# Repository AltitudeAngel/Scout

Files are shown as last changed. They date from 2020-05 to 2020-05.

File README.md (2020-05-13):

# Scout

_Scout_ is an open-source project consisting of hardware and firmware that enables software developers, drone manufacturers and commercial drone pilots to quickly develop drone solutions that collect (using an extensible chip architecture) information about the location of the device (or, the vehicle to which the device is attached), and use cellular communications technologies to both send that position and other sensor data to and receive navigation data back from unmanned traffic management (UTM) system.

Scout's *not* presently aimed at drone pilots or consumers who want an off-the-shelf device to attach to their drone. While a few such devices do exist, we created _Scout_ to address several limitations of these devices: that they're proprietary, work only with a specific service provider (which supports vendor lock-in and reduces market choice), and are generally only 'one-way' (i.e. broadcasting the drone's location over the cellular network to a remote receiver).

_Scout_ is designed to work _in tandem_ with the flight controller or ground control station already responsible for the flight of the drone itself, by augmenting the capability of the control solution with additional information obtained from an unmanned traffic management system, like GuardianUTM by Altitude Angel.

## Why we built _Scout_

With _Scout_, it's possible to connect a drone to a UTM Provider with secure, two-way communications and to _receive_ important safety messages back from the UTM that the drone's control station can respond to, such as:

* Changes to the airspace while you fly (eg. the creation of a NOTAM in-flight)
* Severe weather forecast changes
* Other nearby drones operating in the vicinity (traffic alerts)
* The presence of nearby manned aviation likely to conflict with your current flight path (conflict resolution)

While proprietary devices on the market exist for sending telemetry about a drone's location to a remote provider, that's only a small piece of the overall landscape of services required to support large-scale automated drone operations. Equally, these devices typically only work with a single provider (known as vendor lock-in, which does not facilitate an ecosystem to flourish), and are closed-source. What is necessary to support routine, automated beyond visual line-of-sight drone flights at scale is a richer connection into new and emerging digital traffic management services using an open architecture that can be enhanced and properly scrutinized.

### Scout uses the hardware ecosystem trusted by tens of millions of makers globally

We therefore started _Scout_ on the following principles:

* Use an existing open-source hardware ecosystem
* Use readily-available, 'commercial off-the-shelf' hardware components to minimise build cost, and risk
* Simplify drone connectivity to a UTM and make it open and available to everyone
* Ensure connectivity is two-way, drone to UTM _and_ UTM to drone

_Scout_ is built using the well-developed and well-known [Arduino](https://www.arduino.cc/) ecosystem and commercially available 2G/3G/4G and GPS modem modules. Current support is for the 8-bit AVR microcontroller ([ATMEGA328P](https://www.microchip.com/wwwproducts/en/ATmega328)) in the Arduino Uno and Nano, and the SIMCOM [SIM7100E](https://simcom.ee/modules/lte/sim7100e/) LTE/GNSS modem module, and with the community's help, we'll continue to add support for a wider range of chips and devices in the future.

## Getting Started

:warning: Before you build and fly with Scout, you should keep in mind that in most jurisdictions it is a requirement to keep your drone in your visual line-of-sight at all times. It is important that you use Scout in accordance with local laws, and that you test Scout is suitable before your first flight.

We recognize that most people will want to get up and running quickly. Whilst we love that, it's important to remember that _Scout_ is currently primarily targeted at non-retail users: those with programming and hardware backgrounds, such as manufacturers of ground control systems (GCS), autopilot/flight controller hardware and drone manufacturers themselves. Accordingly, in the earlier versions of the hardware and software, there are a few small hoops you'll need to jump through in order to get up-and-running, and, as in all early-release projects, we're continually adding improvements and tweaks along the way and both welcome and encourage community contributions, too.

### Step one: build your hardware

For now, the shortest sequence of steps to go from this repository to a device that you can fly around with is as follows:

* Build the [hardware](hardware/README.md) and upload the [firmware](firmware/README.md) to the microcontroller
  * [Breadboard Build Guide](hardware/breadboard/BreadboardBuildGuide.md)
  * [Standalone Hardware Build Guide](hardware/pcb/PCBBuildGuide.md)
  * [Case Build Guide](hardware/case/CaseBuildGuide.md)
* You'll also need a SIM card with a data contract from your preferred mobile network operator (noting that not all telecoms operators permit the use of their network at altitude, so do check first).

> Note that you don't _need_ Scout hardware to connect to the UTM Providers listed in this repository. In fact, if you already have a means to provide an internet connection back from your drone to the UTM Provider service, at relatively low latency, then you can skip this part and move straight to software integration.

### Step two: Connect to a supported UTM Provider

_Scout_ is designed to collect location data (which we call a 'position report') and forward it to a UTM system provider over cellular connectivity, working as a 'co-pilot' to help your drone(s) avoid hazardous situations while in-flight. To do this effectively, it's best if you connect it to a UTM Provider that has the necessary APIs and infrastructure in place to receive the telemetry, and provides the capability to send data back to your _Scout_ device (or via another control channel) so that you can respond to the presence of other nearby drones or manned aviation etc.

> Did you know? You can actually build-out your own back-end UTM services if you wish, but you'll need to keep in mind that building scalable infrastructure that's reliable enough to deal with your drone while it is in transit is an important consideration not to be overlooked, as are the services which you'll need to build on top of that infrastructure.

#### Supported UTM Providers

The current firmware supports connectivity into the following UTM Providers:

| UTM Provider | 1-way | 2-way |
| --- | --- | --- |
| [Altitude Angel](https://developers.altitudeangel.com) | Yes | Yes |

NB: You can contribute your own code to provide connection to other UTM Providers, or you can modify the firmware to work directly with your own, non-UTM based system. The choice is yours!

## Roadmap
The initial release of Scout is about providing a low-cost, workable combination of hardware and software to bring UTM to life in real-world scenarios. _Scout_ is based on Altitude Angel's core values of openness and choice in the market, which is why it is offered as open source. Accordingly, you can hook it up to work in almost any scenario and with any cloud platform provider.

### What's next?

The project is currently in release version 0.1, however, we've already set out our next few steps and are encouraging the community to support the project's development further. Below are what we're planning to add support for next:

* Adding I2C bus integration with Altitude Angel's Tactical Conflict Resolution Service (CRS) API
* Support for additional GPS/2G/3G/4G modules
* Hardware designs for a self-contained, battery powered, 3D printable unit
* Additional sensors support including barometer, temperature, humidity, accelerometer, and magnetometer
* Integration with open source drone avionics projects

You can help to shape and influence the direction and roadmap for _Scout_, simply by using it, sharing your feedback and ideas with the rest of the contributors and the community.

# Licence

The Scout firmware is licensed under the [Apache 2.0 licence](https://choosealicense.com/licenses/apache-2.0/#), and the hardware is licensed under [Creative Commons BY-SA](https://creativecommons.org/licenses/by-sa/4.0/).

Made with 💗 by Altitude Angel

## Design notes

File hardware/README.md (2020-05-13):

# Scout Hardware

This directory contains the _hardware plans and schematics_ for the _Scout_ device. You'll also need the firmware to get a fully working device, so head over to the [Scout Firmware](../firmware/README.md) section for the source code and a guide on how to compile and upload the firmware to your device.

Schematic of the Scout hardware on a breadboard

## Getting Started

This guide assumes that you are familiar with building small-scale electronics projects for the [Arduino](https://www.arduino.cc/) platform.

This includes building projects on a breadboard, sourcing and buying electronic components, ordering or manufacturing PCBs (if you're _that_ keen!), and soldering both through-hole and surface mount components. In addition, this directory also contains information on building an enclosure for the Scout device using plans for a 3D printer.

If you want to build the Scout hardware on a breadboard (which is always a good idea to prototype before heading straight to manufacturing) then consult the [Breadboard Build Guide](breadboard/BreadboardBuildGuide.md) to get started.

To build a 'standalone' Scout device based on the plans in this repository that could be securely attached to a drone to provide remote ID, drone telemetry and navigation assistance, then consult the [PCB Build Guide](pcb/PCBBuildGuide.md). For a suitable case for the standalone Scout hardware, consult the [Case Build Guide](case/CaseBuildGuide.md).

:warning: Do keep in mind that this project is open-source, and provided "as-is". We do _not_ recommend that you proceed straight to manufacturing a PCB without first becoming familiar with a working breadboard prototype, and exploring whether the reference designs contained herein are suitable for your specific purposes.

## Overview

There are four main logical parts to the hardware:

- microcontroller;
- cellular modem (which includes, in our design, an onboard GPS/GLONASS sensor);
- user interface; and
- power supply. 

The following sections describe each of these logical parts and how they interact.

## Microcontroller

The brains of the _Scout_ hardware is the microcontroller, which is currently an [ATmega328p](https://en.wikipedia.org/wiki/ATmega328), the same microcontroller at the centre of an Arduino Uno and Nano. This is where the firmware is uploaded to and runs, and is responsible for interfacing with the User Interface components, the Modem Module, and a drone through an I2C bus. 

| The ATmega328p is an 8-bit AVR CPU, with 32KB of flash memory, running at a clock speed of 16 MHz. You might be thinking that this is very low-specification, and you're _completely_ right! Being low-specification doesn't mean low capability, however, and running at such a low clock speed helps power efficiency.

The choice of the Arduino platform for the microcontroller was based also on the large global community and ecosystem of parts around the Arduino project and the wide range of guides and support that already exists. This is the very DNA on which the emergence of drone technology in its earlier years also started to take flight.

In future versions of Scout we'd like to expand the microcontroller options, both to enable both more complex and capable microcontrollers to add additional features, and perhaps even smaller ones too.

## Modem Module

If the microcontroller is the 'brains' of Scout, then the modem module is the mouth and ears! The module we've selected, however, also provides GPS/GLONASS functionality. Thus, in one small, relatively power-efficient chip, you get accurate positioning as well as the 2G/3G/4G modem to provide a two-way communication channel to the UTM provider.

There are many available modem modules available on the market, from many different suppliers and different capabilities and price points. And, as this project is open source, you can also swap out the communications hardware to perhaps opt for satellite communications, or multiple communications streams: it's up to you to pick the combination that works best for your scenario. 

We started out with the Simcom [SIM7100E](https://simcom.ee/modules/lte/sim7100e/), but expect this project to expand the choices available, both to simpler and lower priced options and more complex ones too. The minimum key requirements of the modem module is that it provides GPS positioning and internet connectivity, and it interfaces to Scout via a serial UART and a "Hayes Modem" command set, which the vast majority of available modem modules do.

## User Interface

To enable users to interact with Scout and understand what it's doing it also needs a User Interface, and this is comprised of simple, robust combination of a few switches and LEDs, helping us to minimise complexity and maximise power-efficiency. There is a single power switch to turn the unit on and off, and a 'pairing' button used to initiate pairing and authentication with a compatible UTM Provider. In addition, there are two LEDs: one to indicate the power-up status of the Scout hardware, and the other to indicate the status of the pairing and connection process. 

These LEDs flash at different rates to indicate different states in the hardware:

- Slow - On for 500ms, off for 500ms
- Medium - On for 250ms, off for 250ms
- Fast - On for 100ms, off for 100ms
- Flash - A single pulse for 50ms

| Power LED | Pair LED | Description |
| --- | --- | --- |
| Off | Off | Scout is powered off |
| Slow | - | Establishing communication with the modem module |
| Medium | - | Setting up the modem, synchronizing time, enabling network and GPS |
| Fast | - | Establishing network connection to the backend service |
| Steady | - | Ready to pair or running |
| - | Slow | Pairing is in progress |
| - | Fast | Pairing token obtained, establishing GPS lock, and authenticating to the UTM Provider |
| - | Flash | Indicates a position report has been successfully sent |
| Slow | Slow | Alternate power/pair slow flashing indicates a fatal device error |
| Fast | Fast | Alternate power/pair fast flashing indicates the device is resetting |

## Power Supply

Lastly, like all electronic devices, Scout needs power (but not much!).

If you're building Scout on a breadboard then a simple bench 5VDC 2A power supply will suffice, but when it is standalone and attached to a drone it needs to run from a battery. In theory, you could power Scout from the battery system already on a drone, but unless you're designing your own drone hardware, that's fairly invasive, and is likely to at least invalidate your warranty, and at worst, affect the flight dynamics of your vehicle. 

The battery is also the heaviest component in _Scout_, which is crucial consideration for any airborne device, but also determines the available run time of the device. Getting the balance right can be tricky. The modem module is the biggest consumer of power in Scout, and from it's datasheet needs 5V at up to 2 amps, although we've observed this be more like 2-5W on average in actual operation, so whichever battery cell you end up choosing you should be mindful of the potential current draw.

In the current design, battery power comes from an 18650 Lithium Ion battery. This was initially chosen because they are very readily available and can deliver the current required to power the modem module. However, this is something we intend to change as these batteries are also quite heavy and somewhat over-specified for the typical power requirements of Scout. In the near future Scout will use a pouch type Lithium Polymer battery. These can deliver lower peak currents, but sufficient for Scout with suitable capacities and in a smaller, lighter and slightly safer form to Lithium Ion.

In addition to the battery, the power supply circuitry enables safe charging of the battery through a Micro USB connector and charge controller, protection of the battery from over-charging, under-charging, short circuit and reverse polarity, and lastly a DC-DC converter to supply a constant and stable 5 volts to the microcontroller and modem module.

# Licence

The Scout hardware is licensed under [Creative Commons BY-SA](https://creativecommons.org/licenses/by-sa/4.0/).

Made with 💗 by Altitude Angel

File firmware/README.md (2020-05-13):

# Scout Firmware

Build Status (https://dev.azure.com/altangel/Altitude%20Angel/_build/latest?definitionId=261&branchName=master)

## Before you begin

This directory contains the _firmware_ for the _Scout_ open-source hardware device. Before you can use the firmware, you'll want to have already built the Scout device, either on a breadboard or a PCB. Head over to the [Scout Hardware](../hardware/README.md) section for schematics and a build guide before you begin.

:warning: Do keep in mind that this project is open-source, and is provided "as is". You should verify and test that the firmware is suitable for any specific purpose you have in mind before you use it.

## Getting Started

This guide assumes that you have built a working _Scout_ device and working data connection, and you're ready to upload firmware.

### Overview

_Scout's_ firmware is designed to securely authenticate itself with a remote service and then establish a two-way communication channel between the _Scout_ device and the remote service for the duration of a flight. The channel is two-way so that the remote service can receive telemetry from the device (which includes the device's GPS coordinates) and can then use the telemetry to send back additional data, such as a recommended manoeuvre to avoid a collision.

The possibilities for this type of service are limited only by the capabilities of the remote service sending and receiving data to and from the _Scout_ device, and the way the responses from the remote service are handled.

Below are a few examples of common usage scenarios:

* Tracking a fleet of drones
* Connecting to a UTM Provider to receive near real-time navigation assistance to help you avoid other aircraft, or even changes to airspace restrictions

When connecting to a UTM Provider, the UTM Provider will explain how their service works and what responses will be sent under what conditions, so that as the implementor of the _Scout_ device in your solution, _you_ can decide what action to take if the UTM Provider prompts you to take action to avoid some type of conflict.

In this getting started guide, we're going to initially cover a blend of both scenarios: first, authenticating your device with the Altitude Angel UTM Provider service, and second, exchanging telemetry with it in real-time. In firmware version 0.2, scheduled June, we'll then show you how to _respond_ to data the Altitude Angel service sends to help you avoid collisions, or flying in a restricted area (known as _realtime, dynamic geo-fencing_).

### Picking a UTM Provider

_Scout_ is designed to collect telemetry and forward it to a remote service using cellular connectivity, working as a 'co-pilot' to help your drone(s) avoid hazardous situations while in-flight. To do this effectively, it's best if you connect it to a UTM Provider that has the necessary APIs and infrastructure in place to receive the telemetry, and provides the capability to send data back to your _Scout_ device (or via another control channel) so that you can respond to the presence of other nearby drones or manned aviation etc.

#### Example implementation flow for basic 'network Remote ID' concept, using Scout and Altitude Angel (one-way)

Basic implementation showing use of Scout and Altitude Angel to satisfy network Remote ID concept

#### Example two-way communication flow using Altitude Angel for navigation assistance

Basic implementation showing use of Scout and Altitude Angel to satisfy network Remote ID concept

>> For a detailed guide on each of the above processes, view the [Altitude Angel UTM Provider documentation](doc/AltitudeAngel.md) contained in this repository.

Alternatively, you can build-out your own capability, build your own connector to another UTM service, and connect the _Scout_ device to one of those.

#### Supported UTM Providers

The current firmware supports connectivity into the following UTM Providers:

| UTM Provider | 1-way | 2-way | Getting started guide |
| --- | ----- | ----- | --- |
| [Altitude Angel](https://developers.altitudeangel.com) | Yes | Yes | [Connect Scout to Altitude Angel](doc/AltitudeAngel.md) |

NB: You can contribute your own code to provide connection to other UTM Providers, or you can modify the firmware to work directly with your own, non-UTM based system. The choice is yours!

## Roadmap

The initial release of Scout is about providing a low-cost, workable combination of hardware and software to bring UTM to life in real-world scenarios. _Scout_ is based on Altitude Angel's core values of openness and choice in the market, which is why it is offered as open source and without restriction. Accordingly, you can hook it up to work in almost any scenario and with any cloud platform provider.

### What's next?

The project is currently in release version 0.1, however, we've already set out our next few steps and are encouraging the community to support the project's development further. Below are what we're planning to add support for next:

* Adding I2C bus integration with Altitude Angel's Tactical Conflict Resolution Service (CRS) API
* Support for additional GPS/2G/3G/4G modules
* Hardware designs for a self-contained, battery powered, 3D printable unit
* Additional sensors support including barometer, temperature, humidity, accelerometer, and magnetometer
* Integration with open source drone avionics projects

You can help to shape and influence the direction and roadmap for _Scout_, simply by using it, sharing your feedback and ideas with the rest of the contributors and the community.

# Licence

The Scout firmware is licensed under the [Apache 2.0 licence](https://choosealicense.com/licenses/apache-2.0/#). 

Made with 💗 by Altitude Angel

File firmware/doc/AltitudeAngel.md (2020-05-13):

# Altitude Angel

This document describes how to connect a _Scout_ device to  the [Altitude Angel](https://www.altitudeangel.com/) UTM platform.

## Supported Capabilities

The table below lists the UTM services provided by Altitude Angel, and whether or not the corresponding functionality has yet been implemented in _Scout_. 

| Service | Description | Available on Altitude Angel | Implemented in Scout Firmware |
| --- | --- | --- | --- |
| Surveillance  | Receives position reports from one or more remote sensors, such as _Scout_ devices | Yes | Yes, from v0.1 |
| Strategic CRS | Receives flight plans, pre-flight, and compares them either with your other flight plans or optionally, those received across all of Altitude Angel's network, and helps you to plan-to-avoid conflicts with other drone flights. | Yes | Not yet |
| Tactical CRS  | Responds to position reports sent via _Surveillance_ with instructions to help you avoid a potential collisions with a manned aircraft, other drones, or breaching airspace rules as they change while you fly, under certain conditions. | Yes | Coming in v0.2 |

You can find the full suite of API services offered by Altitude Angel at https://docs.altitudeangel.com/.

## Getting started

The first thing we need to do is to _associate_ a new _Scout_ device with your developer account.

To do this:

1. Go to [Altitude Angel's Developer site](https://developers.altitudeangel.com/) and create a free developer account.

:warning: Please pay attention to the terms and conditions. In particular, note that use of any UTM service is *not* a replacement for your normal legal and professional obligations as a drone pilot.

2. Once setup, [open a support ticket](https://customerportal.altitudeangel.com/) and let us know the email address of your new developer account, requesting authorization to associate a new _Scout_ device (or devices) with your account. You'll first need to know the IMEI number for each of your _Scout_ devices you want to associate (if you have a lot, let us know - and we can help you out so you don't have to specify them all). We aim to arrange all approvals within about a working day, or less.

3. You're all set! You can now send/receive telemetry and navigation support from all of Altitude Angel's UTM services supported by _Scout's_ current firmware, and we'll update this guide shortly to show you several common usage scenarios and how to do this successfully.

## Typical basic Remote ID implementation

In a typical usage scenario, you'll connect your _Scout_ device to Altitude Angel's [Surveillance](https://docs.altitudeangel.com/docs/surveillance-api) API. The basic process for doing this looks like this:

Basic implementation showing use of Scout and Altitude Angel to satisfy network Remote ID concept

By way of exaplanation, in the flow above, we're effectively:

1. Pairing the device with the Altitude Angel Surveillance API
2. Altitude Angel's UTM Services will issue a globally-unique Remote ID to be used for your flight.
3. Sending position reports through the Surveillance API to Altitude Angel, using the Remote ID.
4. Flying!

This is enough for a basic Remote ID implementation!

## Advanced integration with Altitude Angel 

However, using Altitude Angel, you're able to receive navigation assistance during your flight. In this flow, there are lots of possibilities for relaying position reports and receiving data to/from the drone, and if you wish, separating out the transmission channel for position reports so they can originate _direct_ on the drone, and _receive_ instructions from Altitude Angel via your Ground Station, on a separate channel:

Basic implementation showing use of Scout and Altitude Angel to satisfy network Remote ID concept

This scenario features integrations with additional APIs, so you'll also need to:

* Submit a flight plan via strategic CRS for your flight using the Scout device identifier
* Start a flight for the flight plan requesting the tactical CRS service
* Integrate with the tactical CRS service using:
  * Your ground control station, and/or
  * (In an upcoming version of Scout) Directly with your drone avionics via I2C

Submitting flight plans via strategic CRS and getting navigation assistance using the tactical CRS service require some additional set up and integration. If you're interested in understanding more about using these services, don't hesitate to get in touch via the [Customer Portal](https://customerportal.altitudeangel.com/).

#### Pairing your device with your Altitude Angel account

To pair _Scout_: 

1. Open a web browser to the [Surveillance Provisioning Portal](https://surveillance.altitudeangel.com/), sign-in with your developer account, and navigate to _Pair Devices_. 

2. Press and hold the _pair button_ on your Scout device for about 1 second, until the pair LED starts slowly flashing on and off. This indicates pairing is in progress. 

3. Go back to the _Pair Devices_ screen, click on the _Pair_ button next to your device to initiate pairing with your _Scout_ device. This allows your _Scout_ device to request a secure token from the Surveillance platform, which it will then use to authenticate with the service later.

4. When _Scout_ has received a token from the Surveillance API, the pair LED will start flashing faster, and once it has been able to get a GPS lock and successfully report a GPS location to the Surveillance API the pair LED will turn off and only flash each time a report is sent to the Surveillance API, which should be roughly once every second. Note that you may need to go _outside_ in order to obtain a GPS lock.

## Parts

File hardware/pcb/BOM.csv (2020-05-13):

ID | Name | Designator | Footprint | Quantity | Manufacturer Part | Manufacturer | Supplier | Supplier Part | LCSC Assembly
1 | XB3306A | U4 | SOT-23(SOT-23-3) | 1 | XB3306A | Xysemi | LCSC | C154939 | Yes
2 | 22K | R8 | R0603 | 1 | RTT032202FTP | RALEC | LCSC | C103416
3 | USB | USB1 | MICRO-USB-SMD_5P-P0.65-H-F_MICRO5.9MMUSB | 1 | MICRO5.9mmusb | SHOU HAN | LCSC | C393940
4 | TP4056X | U1 | SOP-8_L4.9-W3.9-P1.27-LS6.0-BL-EP | 1 | TP4056X | Nanjing Extension Microelectronics | LCSC | C191323
5 | 16MHz | X1 | OSC-SMD_3P-L3.2-W1.3-P1.2-L | 1 | CSTCE16M0V53-R0 | MuRata | LCSC | C32180
6 | 10uF | C3,C4 | C0603 | 2 | GRM188R61A106KE69D | MuRata | LCSC | C77044
7 | SS34 | D1 | SMB_L4.6-W3.6-LS5.3-L-FD | 1 | SS34 | MDD | LCSC | C13762 | Yes
8 | 1K | R4,R3,R6 | R0603 | 3 | RTT031001FTP | RALEC | LCSC | C103198
9 | PWR | KEY1 | KEY-TH_KAN4562-0501C | 1 | KAN4562-0501C | GANGYUAN | LCSC | C231728
10 | PAIR | KEY2 | KEY-TH_KAN4562-0501C | 1 | KAN4562-0501C | GANGYUAN | LCSC | C231728
11 | 220 | R1,R11 | R0603 | 2 | RTT032200FTP | RALEC | LCSC | C103414
12 | SB6286 | U5 | SOT-23-6_L2.9-W1.6-P0.95-LS2.8-BL | 1 | SB6286 | SHOUDING | LCSC | C157668 | Yes
13 | ICSP | H1 | HDR-TH_6PIN-V-ROW2-COL3-MALE-PITCH2.54 | 1 | Header-Male-2.54_2x3 | BOOMELE | LCSC | C65114
14 | 120 | R2 | R0603 | 1 | RTT031200FTP | RALEC | LCSC | C103247
15 | PWR | LED1 | LED-ARRAY-SMD_0603-4P-L1.6-W1.5-BR-RD | 1 | LTST-C195KGJRKT | Lite-On | LCSC | C125104
16 | CRG | LED2 | LED-ARRAY-SMD_0603-4P-L1.6-W1.5-BR-RD | 1 | LTST-C195KGJRKT | Lite-On | LCSC | C125104
17 | 4.7uH | L1 | IND-SMD_L5.0-W5.0 | 1 | LQH5BPN4R7NT0L | Murata Electronics | LCSC | C171792
18 | 10K | R7,R10 | R0603 | 2 | RTT031002FTP | RALEC | LCSC | C103199
19 | RST | SW1 | KEY-SMD_4P-L3.5-W3.4-P2.20-LS3.9 | 1 | TS-1177-B-A-B | XKB Enterprise | LCSC | C381051
20 | 22uF | C6,C7 | C0603 | 2 | GRM188R61A226ME15D | MuRata | LCSC | C84419
21 | I2C | H2 | HDR-2X1/2.54 | 1 | 826629-2 | TE Connectivity | LCSC | C86471
22 | 3K | R9 | R0603 | 1 | RTT033001FTP | RALEC | LCSC | C103514
23 | FDN337N | Q1 | SOT-23-3_L3.0-W1.7-P0.95-LS2.9-BR | 1 | FDN337N | ON Semicon | LCSC | C241805
24 | 100nF | C5,C8 | C0603 | 2 | GRM188R71C104KA01D | MuRata | LCSC | C45000
25 | 1.2K | R5 | R0603 | 1 | RTT031201FTP | RALEC | LCSC | C103248
26 | ATMEGA328P-AU | U3 | TQFP-32_L7.0-W7.0-P0.80-LS9.0-BL | 1 | ATMEGA328P-AU | MICROCHIP | LCSC | C14877 | Yes

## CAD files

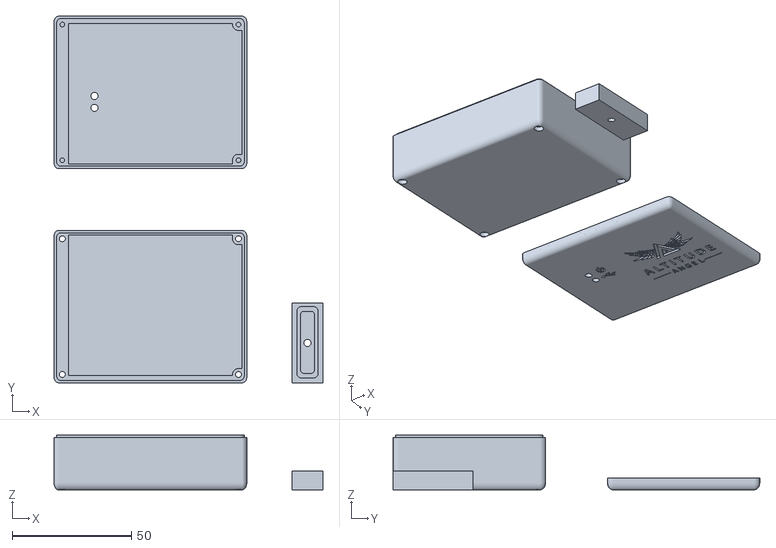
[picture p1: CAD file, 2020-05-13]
hardware/case/ScoutCase.stl
113.0 x 154.0 x 23.0

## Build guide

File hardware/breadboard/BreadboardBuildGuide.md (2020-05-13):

# Breadboard Build Guide
This guide will show you how to build the basic Scout hardware on a breadboard, how to flash the firmware onto microcontroller, and set up debugging the firmware. This will enable you to start experimenting with the hardware and firmware and to debug it.

If you've not built an Arduino on a breadboard before, it is recommended you read and familiarize yourself with the [Building an Arduino on a Breadboard](https://www.arduino.cc/en/Main/Standalone) documentation on the Arduino site first, as much of this guide is based on this.

> Many thanks to [Fritzing](https://fritzing.org/) for the excellent software that enabled us to create the breadboard layout and schematics.

## Parts List

The main Scout hardware on a breadboard requires the following components:

* 1 x Breadboard (0.1" pitch, half+ size - 30x10 contacts with power rails)
* 1 x SIMCOM SIM7100E DevKit board
* 1 x ATMEL ATmega382P-PU (28-pin DIP package)
* 1 x 16Mhz clock crystal
* 2 x 22pF ceramic capacitors
* 1 x 10uF electrolytic capacitor
* 2 x 220Ω resitors
* 1 x 1kΩ resistor
* 1 x Red LED
* 1 x Green LED
* 2 x push button switches
* 1 x toggle switch
* Connecting wire
* +5V power supply capable of delivering up to 2A

For programming the firmware you'll addtionally need:

* 1 x Ardunio Uno
* 1 x 10uF electrolytic capacitor
* Connecting wire
* Computer with the Ardunio IDE installed

And for debugging you'll also need:

* 2 x Serial to USB adapters (FTDI-based or similar)
* Connecting wire

## Layout

The layout of the breadboard is shown in the diagram below, along with the schematic for the circuit. These can also be downloaded in [Fritzing format](../Scout-Fritzing.fzz).

Start by locating the ATMega328P in the middle of the breadboard, as everything connects to this in some way, and then connect wires between the power supply rails and the other components, starting with the low lying components first (switches and connecting wires) and moving on to the raised components to finish (LEDs, resistors, capacitors). Finally, connect the SIM7100E DevKit board (shown on the layout as just a 7-pin header, but will actually hang off the breadboard), and with the power switch in the off position, connect up the power supply to the power supply rails.

Breadboard Layout

Breadboard Schematic

## Programming

Programming the Scout firmware onto the ATMega328P microcontroller uses a separate Arduino as an In-circuit Serial Programmer (ISP). The details of doing this are covered in the [Arduino ISP Tutorial](https://www.arduino.cc/en/Tutorial/ArduinoISP) on the Arduino website. The steps involved are:

* Connect an Arduino Uno to your computer over USB.
* Open the Arduino IDE and open the ArduinoISP sketch from the Examples in the IDE.
* Select the Arduino Uno as the board and the correct serial port to program it, and them compile and upload the ArduinoISP sketch to the Arduino Uno.
* Disconnect your breadboard circuit from your power supply
* Connect your Arduino Uno to your breadboard as follows:
  * ATMega328P pin 1 RESET (breadboard left side, row 8) to Uno digital pin 10
  * ATMega328P pin 17 MOSI (breadboard right side, row 19) to Uno digital pin 11
  * ATMega328P pin 18 MISO (breadboard right side, row 18) to Uno digital pin 12
  * ATMega328P pin 19 SCK (breadboard right side, row 17) to Uno digital pin 13
  * Power rail GND (-) to Uno GND
  * 10uF electrolytic capacitor between Uno GND and Uno RESET (ensure capacitor -ve is connected to GND)
  * Power rail +5V to Uno +5V

Once this is done the Scout firmware can be programmed onto the microcontroller. To do this open the Scout sketch in the Arduino IDE and select Arduino as ISP in the Tools/Programmer menu. Then run the Upload Using Programmer and the sketch will be built and uploaded to the microcontroller. You will know this is complete when the Power LED starts flashing on and off every 500ms, indicating that communications is trying to be established with the modem module.

## Debugging

When developing and debugging the firmware, it is often essential to be able to see the communications between the microcontroller and the modem module. To do this it is simplest to use two serial to USB adapters to monitor the serial communication on the receive and transmit lines between the microscontroller and the modem module. Connect the two serial to USB adapters so that their GND is common with the breadboard power rail GND, and then connect the receive input of one of the adapters to RXD on the microcontroller (ATMega328P pin 2, breadboard left side, row 9), and the other adapter receive input to TXD on the microcontroller  (ATMega328P pin 3, breadboard left side, row 10). Then on your computer you will be able to open up two serial monitors on the two USB adapter COM ports (115200 baud, 8 data bits, 1 stop bit) and watch the communication between the microcontroller and modem module.

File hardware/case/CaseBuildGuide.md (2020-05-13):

# Case Build Guide

A simple case has been designed to house the standalone Scout hardware, including the PCB, battery and module module, and is available in [STL format](ScoutCase.stl). This case can be 3D printed using any suitable 3D printing hardware with a minimum print volume of approximately 180mm x 150mm x 25mm. We have currently tested printing this case using a Creality Ender 3 and black PLA filament, and it works well, but in common with good 3D prints it is important to ensure good bed leveling, a maximum layer height of 0.2mm, and to experiment with extrusion settings to get the best possible finish. This is another area where community input will be valuable by sharing our 3D printer successes and failures and getting good settings that work.

The case includes top holes to enable the LEDs to been seen and side holes to enable access to the power and pair switches and the Micro USB connector for charging. The top LED holes are 3mm in diameter and designed to enable 3mm clear acrylic rod to be glued into them as light guides the to surface mount LEDs on the PCB underneath, and sealing the case from the elements.

Included in the case model is a mould the correct shape for a bung to be created that fits the side of the case to protect the switches and Micro USB connector underneath from the elements. To create this bung, first lightly wet the mould with water and then fill it tightly with silicone sealant. Once full scrape off the top of the mould to get a flat finish and wait for the sealant to dry completely. Once dry it should be possible to pull the silicon from the mould, and it should fit nicely into the recess in the side of the case.

The lid of the case is fixed to the body with 4 x 25mm M2 bolts, and is designed with a lip to both ensure a snug fit to the body and so that silicon sealant could additionally be applied for further waterproofing.

The PCB should be fixed in the case using a 1mm thick foam adhesive pad.

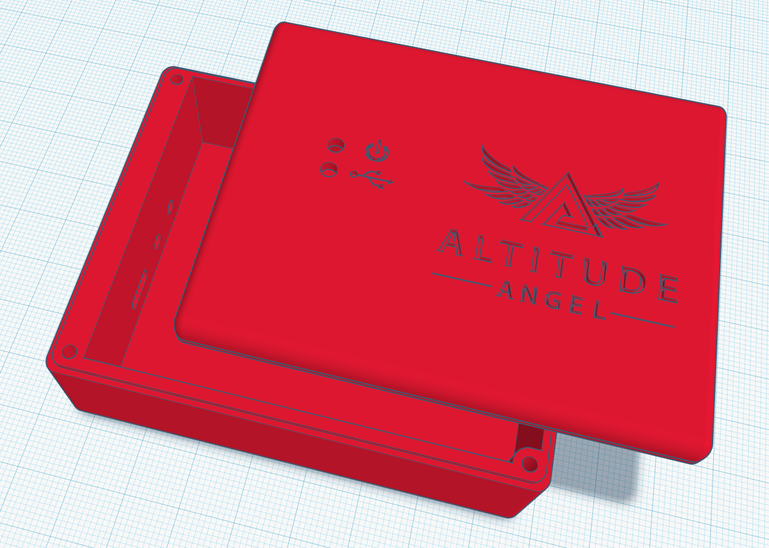
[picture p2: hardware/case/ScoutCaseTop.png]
Case Top Photo


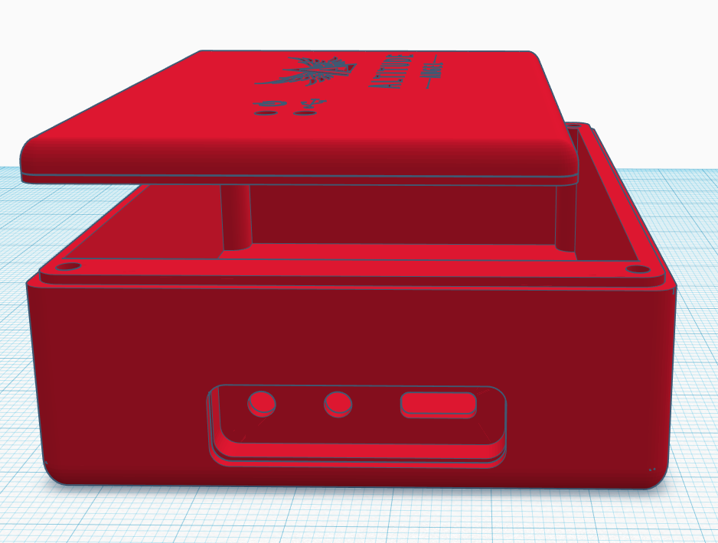
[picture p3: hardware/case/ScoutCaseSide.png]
Case Side Photo


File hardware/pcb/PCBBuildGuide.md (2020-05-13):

# PCB Build Guide

This guide will show you how to build the PCB for the Scout hardware and how to flash the microcontroller on the PCB.

> Many thanks to [EasyEDA](https://easyeda.com/) for the excellent software that enabled us to create the PCB layout and schematics, and prototype PCBs for testing.

## Overview

The design of the PCB is focused on ease of self-assembly and to enable the Scout circuit to be self-contained in a case for mounting to a drone. This brings together the microcontroller and modem module with a Li-Ion battery, MicroUSB charging circuit, battery protection and a DC-DC converter. The design currently uses an 18650 Lithium Ion battery, but it is envisaged that this will become a pouch-based Lithium Polymer battery in future designs to enable the size and weight to be shrunk further. In addition, this iteration of the design uses the off-the-shelf modem module connected via a PCB header, but future designs will integrate this module onto the PCB, again to shrink its size and weight.

* PCB approx. dimensions: 69mm x 59mm x 23mm
* PCB approx. weight, incl. battery: 75g

## Parts List

The parts needed to build the PCB are listed in the table below. These can also be downloaded as a CSV [Bill Of Materials](BOM.csv) and a CSV [Pick And Place](PickAndPlace.csv) specification for manufacturing.

|  Qty | Designators | Manufacturer | Part |
| ---: | --- | --- | --- |
| 1 | U1 | Nanjing | TP4056X (battery charger) |
| 1 | U3 | MICROCHIP | ATMEGA328P-AU |
| 1 | U4 | Xysemi | XB3306A (battery protection) |
| 1 | U5 | SHOUDING | SB6286 (dc-dc power) |
| 1 | Q1 | ON Semicon | FDN337N (mosfet) |
| 1 | D1 | MDD | SS34 |
| 1 | L1 | Murata Electronics | LQH5BPN4R7NT0L |
| 1 | X1 | MuRata | CSTCE16M0V53-R0 (16MHz resonator) |
| 1 | LED1 | Lite-On | LTST-C195KGJRKT |
| 1 | LED2 | Lite-On | LTST-C195KGJRKT |
| 2 | R1,R11 | RALEC | RTT032200FTP |
| 1 | R2 | RALEC | RTT031200FTP |
| 3 | R4,R3,R6 | RALEC | RTT031001FTP |
| 1 | R5 | RALEC | RTT031201FTP |
| 2 | R7,R10 | RALEC | RTT031002FTP |
| 1 | R8 | RALEC | RTT032202FTP |
| 1 | R9 | RALEC | RTT033001FTP |
| 1 | USB1 | SHOU HAN | MICRO5.9mmusb (MicroUSB) |
| 2 | C3,C4 | MuRata | GRM188R61A106KE69D |
| 2 | C6,C7 | MuRata | GRM188R61A226ME15D |
| 2 | C8,C5 | MuRata | GRM188R71C104KA01D |
| 1 | H1 | BOOMELE | Header-Male-2.54_2x3 |
| 1 | H2 | TE Connectivity | 826629-2 |
| 2 | KEY1,KEY2 | GANGYUAN | KAN4562-0501C |
| 1 | SW1 | XKB Enterprise | TS-1177-B-A-B |

## Layout

The overall layout of the PCB is shown in the diagram below, as well as separate files for each of the individual PCB layers, Gerber files for manufacturing, and the schematics for the circuit. These can also be downloaded in [EasyEDA format](../Scout-Scout-EasyEDA.json).

Overall PCB Layout

### PCB Layers 

* [Bottom](BottomLayer.svg)
* [Bottom Solder Mask](BottomSolderMaskLayer.svg)
* [Document](Document.svg)
* [Multi Layer](Multi-Layer.svg)
* [Top](TopLayer.svg)
* [Top Paste Mask](TopPasteMaskLayer.svg)
* [Top Silk](TopSilkLayer.svg)
* [Top Solder Mask](TopSolderMaskLayer.svg)

### Gerber Files

* [Board Outline](Gerber_BoardOutline.GKO)
* [Bottom Layer](Gerber_BottomLayer.GBL)
* [Bottom Solder Mask](Gerber_BottomSolderMaskLayer.GBS)
* [Drill Non-Plated Through Holes](Gerber_Drill_NPTH.DRL)
* [Drill Plated Through Holes](Gerber_Drill_PTH.DRL)
* [Top Layer](Gerber_TopLayer.GTL)
* [Top Paste Mask](Gerber_TopPasteMaskLayer.GTP)
* [Top Silk](Gerber_TopSilkLayer.GTO)
* [Top Solder Mask](Gerber_TopSolderMaskLayer.GTS)

## Schematics

Power and Charge Circuit

Microcontroller Circuit

## Programming

Programming the Scout firmware onto the ATMega328P microcontroller is very similar to programming on a breadboard and uses a separate Arduino as an In-circuit Serial Programmer (ISP). The details of doing this are covered in the [Arduino ISP Tutorial](https://www.arduino.cc/en/Tutorial/ArduinoISP) on the Arduino website. The steps involved are:

* Connect an Arduino Uno to your computer over USB.
* Open the Arduino IDE and open the ArduinoISP sketch from the Examples in the IDE.
* Select the Arduino Uno as the board and the correct serial port to program it, and them compile and upload the ArduinoISP sketch to the Arduino Uno.
* Disconnect your PCB circuit from the battery or Micro USB
* Connect your Arduino Uno to your PCB using the ICSP header (H1) follows:
  * ICSP pin 5 RST to Uno digital pin 10
  * ICSP pin 4 MOSI (breadboard right side, row 19) to Uno digital pin 11
  * ICSP pin 1 MISO (breadboard right side, row 18) to Uno digital pin 12
  * ICSP pin 3 SCK (breadboard right side, row 17) to Uno digital pin 13
  * ICSP pin 6 GND (-) to Uno GND
  * 10uF electrolytic capacitor between Uno GND and Uno RESET (ensure capacitor -ve is connected to GND)
  * ICSP pin 2 VCC to Uno +5V

```
AVR ICSP 6-pin Header
     /---+---+
MISO | 1 | 2 | VCC
     +---+---+
 SCK | 3 | 4 | MOSI
     +---+---+
 RST | 5 | 6 | GND
     +---+---+
```  

Once this is done the Scout firmware can be programmed onto the microcontroller. To do this open the Scout sketch in the Arduino IDE and select Arduino as ISP in the Tools/Programmer menu. Then run the Upload Using Programmer and the sketch will be built and uploaded to the microcontroller. You will know this is complete when the Power LED starts flashing on and off every 500ms, indicating that communications is trying to be established with the modem module.

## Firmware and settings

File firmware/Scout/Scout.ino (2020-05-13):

#include <Arduino.h>
#include <avr/pgmspace.h>
#include <time.h>

// #define USE_TEST_METHODS
// #define USE_POWER_OFF_FIRST
// #define USE_POWER_ON
// #define USE_ACTIVE_GPS_ANTENNA
// #define ACTIVE_GPS_ANTENNA_MILLIVOLTS 3050
#define USE_HTP_TIME_SYNC

#include "Error.h"
#include "Hardware.h"
#include "Settings.h"
#include "Http.h"
#include "PositionReport.h"

#define MODEM_APN "giffgaff.com"
#define MODEM_USERNAME "giffgaff"
#define MODEM_PASSWORD ""

#define POSITION_INTERVAL 1000
#define PAIR_INTERVAL 1000
#define PAIR_TIMEOUT 60000L
#define PAIR_EXPIRY_MIN_SEC 60L * 60L
#define PAIR_EXPIRY_MAX_SEC 24L * 60L * 60L
#define HTTP_OK 200
#define HTTP_ACCEPTED 202
#define HTTP_UNAUTHORIZED 401
#define HTTP_NOT_FOUND 404
#define MAX_FAILED_AUTH 3
#define SCOUT_USER_AGENT F("AltitudeAngelScout/1.0.0")
#define MIME_CONTENT_TYPE_JSON F("application/json")
#define AUTHORIZATION_BEARER F("Bearer ")
#define SURVEILLANCE_API "surveillance-api.altitudeangel.com"
#define PAIR_URI_PREFIX F("/v1/pairing-tokens/consume-token?clientUniqueId=imei:")
#define REPORT_URI F("/v1/position-reports")

static char ACCESS_TOKEN_JSON[] = "\"accessToken\":";
static size_t ACCESS_TOKEN_JSON_LEN = strlen(ACCESS_TOKEN_JSON);
static char EXPIRES_AT_JSON[] = "\"expiresAt\":";
static size_t EXPIRES_AT_JSON_LEN = strlen(EXPIRES_AT_JSON);

unsigned long reportId = 0;

void setup() {
  // Hook timer 0 to manage LED flashing and button presses
  OCR0A = 0xAF;
  TIMSK0 |= _BV(OCIE0A);

  // Set up pin modes not covered by LEDs or Buttons
  pinMode(PIN_MODEM_TX, INPUT);
  pinMode(PIN_MODEM_RX, OUTPUT);
  pinMode(PIN_MODEM_PWR, OUTPUT);
  pinMode(PIN_MODEM_SLP, OUTPUT);

  // Set up button press durations
  pairButton.setShortPress(BTN_SHORT_PRESS);
  pairButton.setLongPress(BTN_LONG_PRESS);

  // Start serial comms to modem at default baud and set timeout
  MODEM_SERIAL.begin(MODEM_DEFAULT_BAUD);
  MODEM_SERIAL.setTimeout(MODEM_TIMEOUT);
  modemStream.setTimeout(MODEM_TIMEOUT);
  do {
    delay(1);
  } while (!MODEM_SERIAL);
  delay(100);
  MODEM_SERIAL.flush();

  // SLP should stay LOW whilst on
  digitalWrite(PIN_MODEM_SLP, LOW);

#ifdef USE_POWER_OFF_FIRST
  // Off = LOW for >= 2500ms then HIGH
  digitalWrite(PIN_MODEM_PWR, HIGH);
  delay(1000);
  digitalWrite(PIN_MODEM_PWR, LOW);
  delay(2600);
#endif
#ifdef USE_POWER_ON
  // On = LOW for >= 500ms then HIGH
  digitalWrite(PIN_MODEM_PWR, HIGH);
  delay(1000);
  digitalWrite(PIN_MODEM_PWR, LOW);
  delay(600);
#endif

  // PWR should stay HIGH whilst on
  digitalWrite(PIN_MODEM_PWR, HIGH);
}

SIGNAL(TIMER0_COMPA_vect)
{
  // Update the LED states
  powerLed.update();
  pairLed.update();

  // Update the button states
  pairButton.update();
}

void loop() {
  // Start the power LED flashing at a slow rate to indicate loop start
  powerLed.setInterval(LED_FLASH_SLOW);
  pairLed.setOff();

  // Try to get serial communications with the modem
  RETRY(modem.getAlive(), "MODEM");

  // Serial communication established so flash the power LED medium
  powerLed.setInterval(LED_FLASH_MEDIUM);

  // Ensure modem is using default settings
  RETRY(modem.setDefaults(), "DEFAULT");
  RETRY(modem.setUserDefaults(), "DEFAULT");

  // Set echo off
  RETRY(modem.setEcho(false), "ECHO");

  // Ensure modem is in full functionality
  RETRY(modem.setFunctionality(1), "FUNC");

  // Get the modem IMEI
  String imei;
  RETRY(modem.getIMEI(imei), "IMEI");

#ifdef USE_TEST_METHODS
  // Get the modem IMSI
  String imsi;
  RETRY(modem.getIMSI(imsi), "IMSI");
#endif

#ifdef USE_TEST_METHODS
  // Get the modem info
  String info;
  RETRY(modem.getInfo(info), "INFO");
#endif

  // Set automatic time updates
  RETRY(modem.setAutoTimeUpdate(true), "TIME");

  // Configure the network
  byte profile = 1;
  RETRY(modem.setNetworkAPN(profile, MODEM_APN, 0, 0), "APN");
  RETRY(modem.setNetworkAuth(profile, 1, MODEM_USERNAME, MODEM_PASSWORD), "AUTH");
  RETRY(modem.setNetworkProfile(profile, true), "PROON");

  // Ensure the network is stopped
  byte netstate;
  RETRY(modem.getNetworkAlive(netstate), "GETNET");
  if (netstate != 0) {
    RETRY(modem.stopNetwork(), "STOPNET");
  }

  // Start the network
  RETRY(modem.setNetworkMode(false), "SETMODE");
  RETRY(modem.setIPSendMode(true), "SETSEND");
  RETRY(modem.startNetwork(), "STARTNET");
  RETRY(modem.getNetworkAlive(netstate) && netstate == 1, "NET");
  
#ifdef USE_TEST_METHODS
  // Get the local IP address
  String ipAddress;
  RETRY(modem.getLocalIPAddress(ipAddress), "GETIP");
#endif

#ifdef USE_HTP_TIME_SYNC
  // Remove any existing HTP servers
  while (true) {
    String servers;
    modem.getHTPServers(servers);
    servers.trim();
    if (servers.length() == 0) break;
    modem.delHTPServer(0);
  }

  // Set the HTP server and update time from HTP
  RETRY(modem.addHTPServer(SURVEILLANCE_API, 80), "HTPADD");
  RETRY(modem.setTimeFromHTP(), "HTPSET");
#endif // USE_HTP_TIME_SYNC

  // Set the GPS antenna power
#ifdef USE_ACTIVE_GPS_ANTENNA
  RETRY(modem.setGPSAntennaVoltage(ACTIVE_GPS_ANTENNA_MILLIVOLTS), "GPSVOLT");
  RETRY(modem.setGPSAntennaPower(true), "GPSPOW");
#else
  RETRY(modem.setGPSAntennaPower(false), "GPSPOW");
#endif

  // Start GPS
  if (!modem.getGPSAlive()) {
    // Not started so start
    modem.startGPS();
    RETRY(modem.getGPSAlive(), "GPS");
  }
  
  // Get common channel state
  byte network, session0, session1;
  RETRY(modem.getCommonChannelState(network, session0, session1), "CC");

  // Ensure the common channel is stopped
  if (network != 0) {
    modem.setCommonChannelClose(0);
    modem.setCommonChannelClose(1);
    RETRY(modem.stopCommonChannel(), "CCSTOP");
  }
  RETRY(modem.getCommonChannelState(network, session0, session1) && network == 0, "CCOFF");

  // Configure the common channel
  RETRY(modem.setCommonChannelMode(false), "CCMODE");
  RETRY(modem.setCommonChannelParam(false, true), "CCPARAM");

  // Start the common channel
  RETRY(modem.startCommonChannel(), "CCSTART");
  RETRY(modem.getCommonChannelState(network, session0, session1) && network == 4, "CCON");
  RETRY(modem.getCommonChannelState(network, session0, session1) && network == 4 && session0 == 1 && session1 == 1, "CCRDY");

  // GPS, network and common channel started so flash the power LED fast
  powerLed.setInterval(LED_FLASH_FAST);

  // Run loop
  unsigned long last = millis();
  byte session = 0;
  unsigned long pairStart = 0;
  bool paired = false;
  int failedAuth = 0;
  while (true) {
    // Only loop each interval
    unsigned long now = millis();
    if (now - last < POSITION_INTERVAL) {
      delay(POSITION_INTERVAL / 10);
      continue;
    }
    last = now;

    // Get the channel stream for the session we're currently using
    CaptureStream *channel = modem.getCommonChannelStream(session);
    Http http(channel);
  
    // Ensure SSL session is established correctly
    if (modem.getCommonChannelState(network, session0, session1)) {

      // Check if network is down and if it is reset by breaking out and restarting the main loop
      if (network != 4) {
        // Full device reset
        break;
      }

      // Get the state or the current and other sessions
      byte currentState = session == 0 ? session0 : session1;
      byte otherState = session == 0 ? session1 : session0;

      // Ensure the other session is closed and ready
      if (otherState != 1) {
        modem.setCommonChannelClose(session == 0 ? 1 : 0);
      }

      // Ensure the current session is connected
      if (currentState != 4) {
        powerLed.setInterval(LED_FLASH_FAST);
        modem.setCommonChannelOpen(session, SURVEILLANCE_API, 443, 2);
        continue;
      }

      // SSL established so turn on the power LED
      powerLed.setOn();
    }

    // If we're not paired see if the stored token is valid to use
    if (!paired) {
      // Read clock
      time_t now;
      if (modem.getClock(now)) {
        // Check if the currently stored token has enough time left on it without needing to pair
        time_t diff = SETTINGS.getTokenExpire() - now;
        if (diff > PAIR_EXPIRY_MIN_SEC && diff < PAIR_EXPIRY_MAX_SEC && SETTINGS.checkToken()) {
          paired = true;
          failedAuth = 0;
          pairLed.setInterval(LED_FLASH_FAST);
        }
      }
    }

    // Attempt to pair if the pair button is long pressed
    if (pairButton.isLongPressed()) {
      // Starting flashing the pair LED as we pair
      pairLed.setInterval(LED_FLASH_SLOW);
      pairStart = millis();
    }

    // If we're pairing attempt to get a token
    if (pairStart > 0) {
      // Check if we've timed out
      if (millis() - pairStart > PAIR_TIMEOUT) {
        pairStart = 0;
        pairLed.setOff();
        continue;
      }

      // Make request for token
      channel->flush();
      String uri(PAIR_URI_PREFIX);
      uri += imei;
      http.sendRequestLine(HTTP_METHOD_POST, uri);
      http.sendRequestHeader(HTTP_HEADER_HOST, SURVEILLANCE_API);
      http.sendRequestHeader(HTTP_HEADER_CONNECTION, HTTP_HEADER_CONNECTION_KEEP_ALVE);
      http.sendRequestHeader(HTTP_HEADER_USER_AGENT, SCOUT_USER_AGENT);
      http.sendRequestHeader(HTTP_HEADER_CONTENT_TYPE, MIME_CONTENT_TYPE_JSON);
      http.sendRequestHeader(HTTP_HEADER_CONTENT_LENGTH, String(0));
      http.sendRequestBody();
      http.sendRequestEnd();
      channel->flush();

      // Read HTTP status
      uint16_t status = 0;
      String description;
      if (!http.recvResponseLine(status, description)) continue;
      switch (status) {
        case HTTP_OK:
          break;
        //case HTTP_NOT_FOUND:
        default:
          channel->flush();
          delay(PAIR_INTERVAL);
          continue;
      }

      // Read till body
      String name, value;
      while (http.recvResponseHeader(name, value));
      if (!http.recvResponseBody()) continue;

      // Read till access token
      if (!channel->find(ACCESS_TOKEN_JSON, ACCESS_TOKEN_JSON_LEN)) continue;

      // Set access token in settings
      pairLed.setInterval(LED_FLASH_FAST);
      SETTINGS.setToken(channel);

      // Read till token expiry
      if (!channel->find(EXPIRES_AT_JSON, EXPIRES_AT_JSON_LEN)) continue;

      // Get expiry data
      String expiry;
      if (!channel->find('"')) continue;
      channel->startCapture(&expiry);
      if (!channel->find('"')) continue;
      channel->stopCapture();

      // Set expiry in settings
      SETTINGS.setTokenExpire(getTokenExpireTime(expiry));

      // Read to the end
      http.recvResponseEnd();

      // Set paired
      paired = true;
      pairStart = 0;
      failedAuth = 0;
    }

    // If paired get and send GPS location
    if (paired) {
      // Read clock
      tm clock;
      clock.tm_year = 0;
      long tz = 0;
      if (!modem.getClock(clock, tz)) continue;

      // Read GPS location
      double lat = 0, lng = 0, alt = 0, speed = 0, course = 0;
      if (!modem.getGPSInfo(lat, lng, alt, speed, course)) continue;

      // Check if we have at least a clock and GPSVOLT
      if (clock.tm_year == 0 || (lat == 0 && lng == 0 && alt == 0 && speed == 0 && course == 0)) {
        continue;
      }

      // Start building a position report
      PositionReport report;
      report.setSensorId(imei);
      report.setId(reportId++);
      report.setPosition(lat, lng);
      report.setTimestamp(clock);

      // Read voltage
      float voltage;
      if (modem.getVoltage(voltage)) {
        report.setVoltage(voltage);
      }

      // Read temperature
      int temperature;
      if (modem.getTemperature(temperature)) {
        report.setTemperature(temperature);
      }

      // Get signal quality
      byte rssi, ber;
      if (modem.getSignalQuality(rssi, ber)) {
        report.setRssi(rssi);
        report.setBer(ber);
      }

      // TODO: Convert speed and course to velocity vector

      // Send the HTTP POST header and position report
      channel->flush();
      http.sendRequestLine(HTTP_METHOD_POST, REPORT_URI);
      http.sendRequestHeader(HTTP_HEADER_HOST, SURVEILLANCE_API);
      http.sendRequestHeader(HTTP_HEADER_CONNECTION, HTTP_HEADER_CONNECTION_KEEP_ALVE);
      http.sendRequestHeader(HTTP_HEADER_USER_AGENT, SCOUT_USER_AGENT);
      http.sendRequestHeader(HTTP_HEADER_CONTENT_TYPE, MIME_CONTENT_TYPE_JSON);
      http.sendRequestHeader(HTTP_HEADER_CONTENT_LENGTH, String(report.length()));
      http.sendRequestHeader(HTTP_HEADER_AUTHORIZATION, AUTHORIZATION_BEARER, SETTINGS.getToken());
      http.sendRequestBody();
      report.writeJson(channel);
      channel->flush();

      // Wait for a response
      uint16_t status = 0;
      String description;
      if (!http.recvResponseLine(status, description)) continue;
      channel->flush();
      switch (status) {
        case HTTP_ACCEPTED:
          break;
        case HTTP_UNAUTHORIZED:
          failedAuth++;
          if (failedAuth > MAX_FAILED_AUTH) {
            paired = false;
            pairLed.setOff();
          }
          continue;
        default:
          continue;
      }

      // Flash the pair LED
      pairLed.setFlash(LED_FLASH_PING);
    }
  }
}

time_t getTokenExpireTime(String expire) {
  tm convert;
  convert.tm_year = expire.substring(0, 4).toInt() - 1900;
  convert.tm_mon = expire.substring(5, 7).toInt() - 1;
  convert.tm_mday = expire.substring(8, 10).toInt();
  convert.tm_hour = expire.substring(11, 13).toInt();
  convert.tm_min = expire.substring(14, 16).toInt();
  convert.tm_sec = expire.substring(17, 19).toInt();
  time_t time =  mktime(&convert);
  return time;
}

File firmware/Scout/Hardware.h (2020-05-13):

#ifndef __HARDWARE_H
#define __HARDWARE_H

#include "ModemStream.h"
#include "Modem.h"
#include "Led.h"
#include "Button.h"

// Pins
#define PIN_MODEM_TX 0
#define PIN_MODEM_RX 1
#define PIN_MODEM_PWR 2
#define PIN_MODEM_SLP 3
#define PIN_BTN_PAIR 6
#define PIN_LED_PWR 7
#define PIN_LED_PAIR 8

// Modem
#define MODEM_SERIAL Serial
#define MODEM_TIMEOUT 1000
#define MODEM_RETRIES 60
#define MODEM_DEFAULT_BAUD 115200L
ModemStream modemStream(&MODEM_SERIAL);
Modem modem(&modemStream);

// LEDs
#define LED_FLASH_SLOW 500
#define LED_FLASH_MEDIUM 250
#define LED_FLASH_FAST 100
#define LED_FLASH_PING 50
Led powerLed(PIN_LED_PWR);
Led pairLed(PIN_LED_PAIR);

// Buttons
#define BTN_SHORT_PRESS 200
#define BTN_LONG_PRESS 2000
Button pairButton(PIN_BTN_PAIR);

#endif //__HARDWARE_H

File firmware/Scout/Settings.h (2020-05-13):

#ifndef __SETTINGS_H
#define __SETTINGS_H

#include <Stream.h>

#define OFFSET_MAX 1000
#define OFFSET_TOKEN_EXPIRE 0
#define OFFSET_TOKEN OFFSET_TOKEN_EXPIRE + sizeof(time_t)
#define CHECK_MAX OFFSET_TOKEN + 20

class Settings {

  private:
    int writeIdx;

    static void captureToEEPROM(uint8_t read, void* state);

  public:
    Settings();
    time_t getTokenExpire();
    void setTokenExpire(time_t expiry);
    int setToken(Stream *stream);
    Stream* getToken();
    bool checkToken();
};

static Settings SETTINGS;

#endif // __SETTINGS_H
